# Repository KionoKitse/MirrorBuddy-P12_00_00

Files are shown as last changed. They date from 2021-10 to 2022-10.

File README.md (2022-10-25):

### Description 
A project to automate power mirrors. The system will detect who is driving based on their seat position. From this, the system will automatically adjust the mirror position based on the detected user's known preferences. Additionally the system will be able to learn new settings if a user has decided to manually adjust the mirror position. 

### Hardware in use
* 1X ATmega328 (Arduino Pro Mini)
* 1X YX-X801 (low voltage cutoff)
* 2X ATtiny85 (micro processor)
* 3X L7805CV (voltage regulator)
* 4X OH137 (hall Sensor)
* 3X MAX485 (RS485 communication modules)

### What's next
* Get ATTiny85 to send a number via RS485 and display it on Arduino with OLED
* Get ATTiny85 to send the values in the correct format
* Design circuit boards  
 
### Progress log 
<details>
	<summary>Details of the project history</summary>
	
* 2021-10-05 Started the GitHub repository
* 2021-10-06 OLED test with Pro Mini
* 2021-10-07 Tested transmitting a value from ATtiny85 to ATmega328 over RS485 and displayed with OLED
* 2021-10-13 Building a RS485 HAT to ease testing
* 2021-10-18 Got the plotter working
* 2021-10-18 Monitor hall over serial working fine
* 2022-10-09 Hall sensor reading from spare housing
* 2022-10-10 Working on code to count number of rotations
* 2022-10-10 ATtiny with peakdetection and softserial
* 2022-10-11 Determined that peak detection uses too much memory "Global variables use 489 bytes (95%) of dynamic memory"
* 2022-10-12 Created a simpler peak detection algorithm 
* 2022-10-13 Added a debounce setting to MonitorHall it seems to be sending counts as expected 
* 2022-10-14 Added code to monitor 2 hall sensors 
* 2022-10-16 Built a relay board that can control the motors 
* 2022-10-17 Working on code to control relay board
* 2022-10-24 Soldered the relay board into the wiring harness
* 2022-10-24 There is some issue with the relay board everything shorts to ground when adjusting the switch
* 2022-10-25 Added a KiCad model to the project
</details>

### Notebook
<details>
	<summary>Next steps</summary>
	
* Voltage divider to sense mirror controls
* Test inputs from mirror switch
* Check for noise with 5V regulator on bench
* Check voltage stability in the car with regulator
* Check if we can run without voltage regulators on each mirror
* ProMini turn on motors then turn off after correct number of rotations achieved 
* Test with multiple MAX485 modules on the network
* Build sample module with ATTiny85
</details>

<details>
	<summary>Notes on the project</summary>
	
* Best to have ATTiny85 keep track of count in case ATmega328 misses a count
* Would be nice to see the actual values that got triggered for data monitoring
* RS485 only send a byte so that makes it challenging for sending an int
* Plotting with RS485 seems too slow
* Would be interesting to see if the MAX485 module could do TX/RX might make calibration easier
* Does rail voltage affect the hall sensors? If so then maybe it would be good to only calibrate them after the voltage has stabilized. 
</details>

<details>
	<summary>Overview</summary>
	
- ProMini is the controller
	* It will detect which diver is in the seat
	* It will detect if the driver has adjusted the mirror
	* It will activate the controls to adjust the mirrors to the correct place
	* Data received
		+ The proMini will be receiving a value that is between 0-255 that contains the limit data and count
		+ It will know which ATtiney is sending because it will be controlling the power to the mirrors
		+ It will also know who is sending because it will have a sensor to detect which way the mirror button is pointing if the user is manually adjusting the mirror position
		+ In the case that the magnet stops in front of the hall sensor then the ATtiny will be sending sporadic readings
		+ There will need to be some sort of way to filter out this noise or adjust the mirrors a little bit to avoid this
- ATtiny85 1&2 are the sensors that monitor the position of the mirrors
	* They will send a signal when the limit switches have been activated
	* They will sens a signal when the hall sensors have detected the magnet passing
	* The RS485 sends a byte of data so that 0-255
	* Data sent
		+ 100 is limit switch for sensor 1 is hit
		+ 200 is limit switch for sensor 2 is hit
		+ 150 is 50 rotations on sensor 1 counted
		+ 255 is 55 rotations counted on sensor 2
	* The count on sensors is reset after 2 seconds of not seeing the hall sensor move
	* There should be some way to calibrate the threshold for the hall sensor reading
	* When it gets power (car turned on) the ProMini will move the mirrors to their outer limits
	* While this is happening the ATtiny85 will be recording the values detected
	* The ProMini will stop and wait a few seconds
	* When the ATtiny detects that it hasn't moved in a while it will use a filter on the collected data to determine the cutoff threshold
	* This data will be sent to the ProMini for logging and the threshold will be set
	* After this data has been sent the ProMini will know that it is okay to move the mirrors into possition
</details>

<details>
	<summary>Collision avoidance</summary>
	
- Collisions are avoided because the ProMini will only be controlling one ATtiny85 at a time so only one node will be transmitting at a time
- It would be impossible for both nodes to be transmitting since the user can only move one mirror at a time
</details>

<details>
	<summary>General thoughts</summary>
	
- Having the ProMini being the controller will allow me to make fine adjustments without having to pull the mirrors off
- limit switches
	* It could be problematic to use the limit switches since they could easily get water damaged since they are exposed to the elements quite a lot. It would be beneficial not not have to rely on them.
	* If I was doing this again I would not have added them since I could easily drive the motors out until I'm sure I'm at the outside limit and then work backwards from there.
	* The inside limit puts stress on the plastic nuts but the outside limit does not
	* Perhaps it's better to not use the limits at all
</details>

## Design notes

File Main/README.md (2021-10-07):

### Description 
In this test the ATTiny85 reads the value of the potentiometer and converts it to a value between 1-180. Then it passes this value over the software serial to the MAX485. A MAX485 on the other side gets the number and sends it to at ATmega328p which displays the value on an SPI OLED screen.

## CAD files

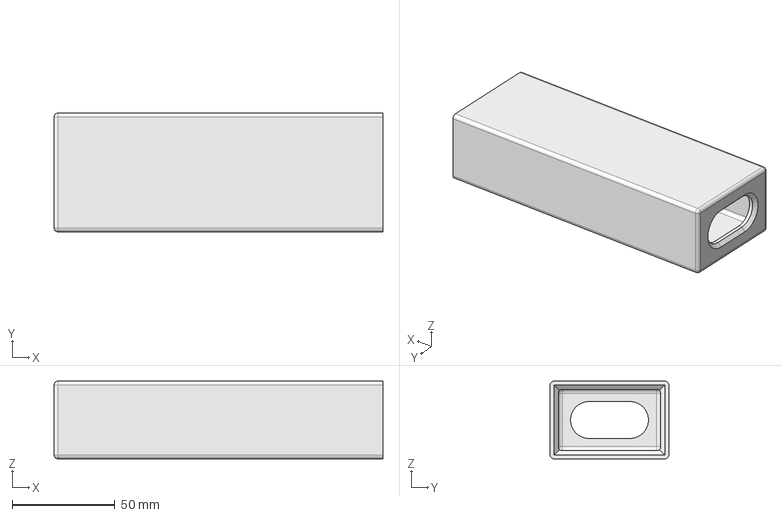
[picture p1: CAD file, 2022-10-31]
Tests/temp/PartB.FCStd
160.5 x 58.0 x 38.0 mm

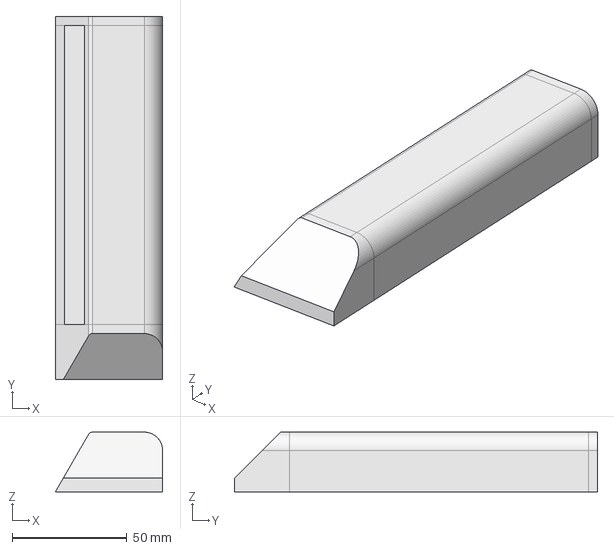
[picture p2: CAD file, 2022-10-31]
Tests/temp/PartA.FCStd
46.7 x 158.0 x 26.0 mm

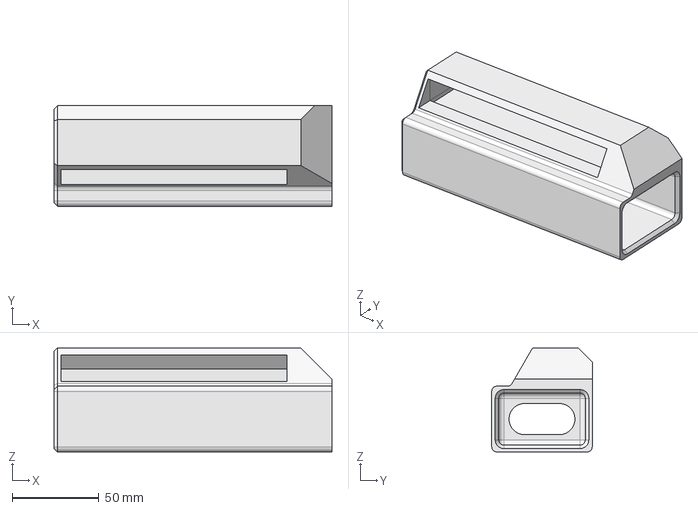
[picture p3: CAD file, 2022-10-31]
Tests/temp/support.FCStd
160.4 x 58.0 x 60.0 mm

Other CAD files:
Tests/temp/PartA.stl
Tests/temp/PartB.stl

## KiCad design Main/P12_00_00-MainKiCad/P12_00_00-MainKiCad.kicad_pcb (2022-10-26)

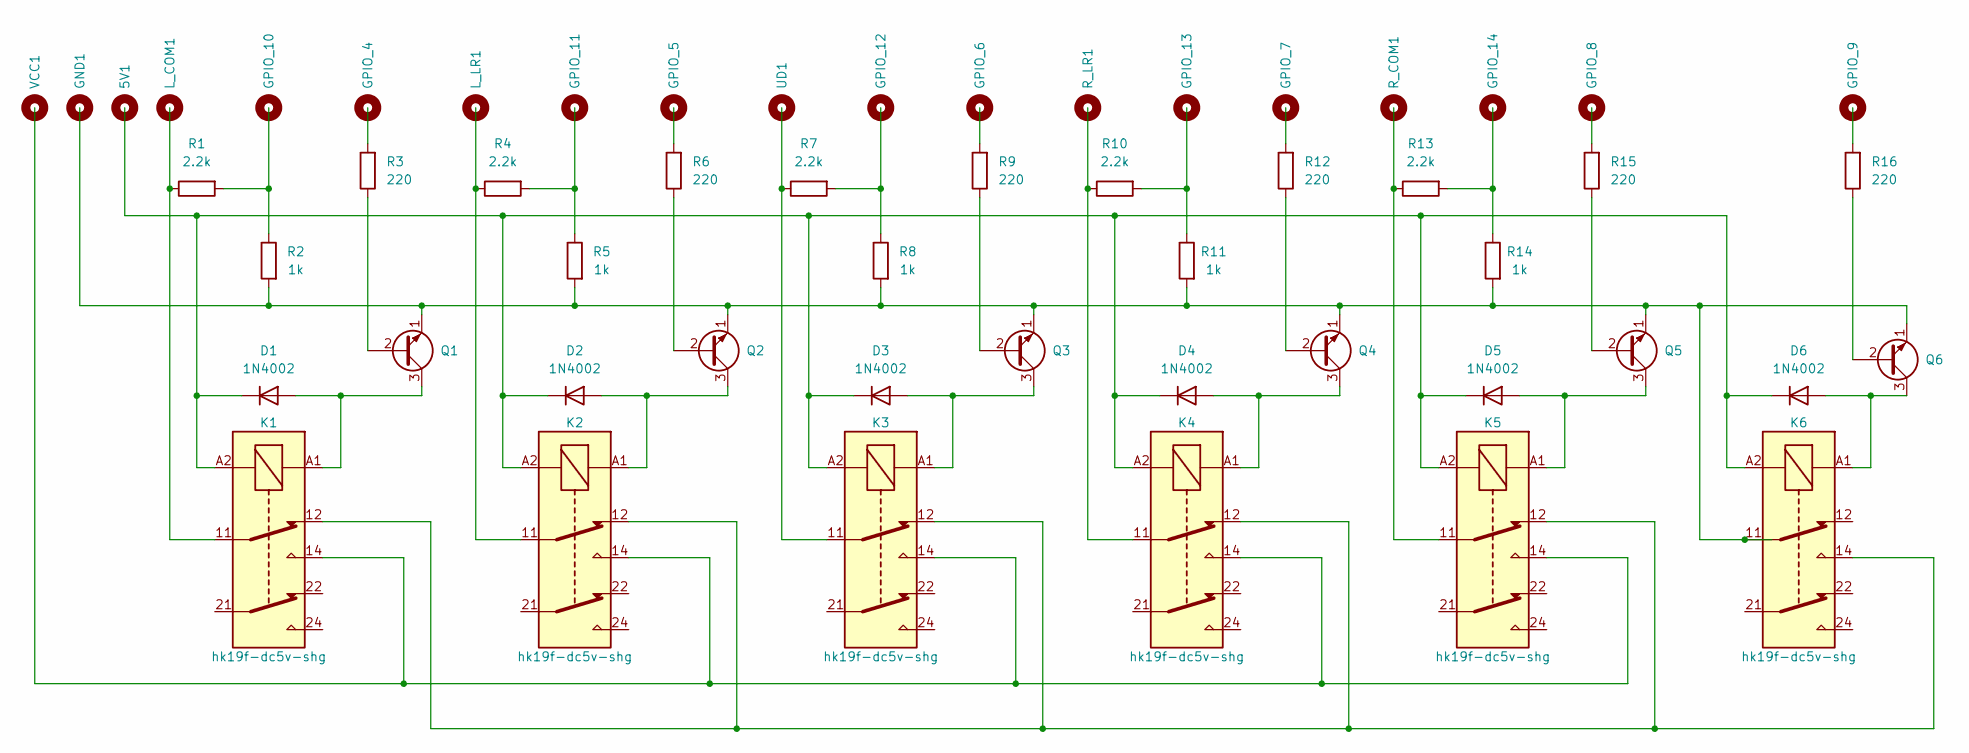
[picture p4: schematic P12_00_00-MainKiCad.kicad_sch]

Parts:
5V1: L_COM; MountingHole_2.1mm
D1, D2, D3, D4, D5, D6: 1N4002; D_DO-34_SOD68_P7.62mm_Horizontal
GND1: L_COM; MountingHole_2.1mm
GPIO_4, GPIO_5, GPIO_6, GPIO_7, GPIO_8, GPIO_9, GPIO_10, GPIO_11, GPIO_12, GPIO_13, GPIO_14: L_COM; MountingHole_2.1mm
K1, K2, K3, K4, K5, K6: hk19f-dc5v-shg; Relay_DPDT_Schrack-RT2-FormC_RM5mm
L_COM1: L_COM; MountingHole_2.1mm
L_LR1: L_COM; MountingHole_2.1mm
Q1, Q2, Q3, Q4, Q5, Q6: 2N3904; TO-92_Inline
R1, R4, R7, R10, R13: 2.2k; R_Axial_DIN0204_L3.6mm_D1.6mm_P5.08mm_Horizontal
R2, R5, R8, R11, R14: 1k; R_Axial_DIN0204_L3.6mm_D1.6mm_P5.08mm_Horizontal
R3, R6, R9, R12, R15, R16: 220; R_Axial_DIN0204_L3.6mm_D1.6mm_P5.08mm_Horizontal
R_COM1: L_COM; MountingHole_2.1mm
R_LR1: L_COM; MountingHole_2.1mm
UD1: L_COM; MountingHole_2.1mm
VCC1: L_COM; MountingHole_2.1mm

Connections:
unnamed: D1.1 (K), D2.1 (K), D3.1 (K), D4.1 (K), D5.1 (K), D6.1 (K), K1.A2, K2.A2, K3.A2, K4.A2, K5.A2, K6.A2
unnamed: D1.2 (A), K1.A1, Q1.3 (C)
unnamed: K1.11, R1.1
unnamed: K1.12, K2.12, K3.12, K4.12, K5.12, K6.14
unnamed: K1.14, K2.14, K3.14, K4.14, K5.14
unnamed: D2.2 (A), K2.A1, Q2.3 (C)
unnamed: D3.2 (A), K3.A1, Q3.3 (C)
unnamed: D4.2 (A), K4.A1, Q4.3 (C)
unnamed: D5.2 (A), K5.A1, Q5.3 (C)
unnamed: D6.2 (A), K6.A1, Q6.3 (C)
unnamed: K6.11, Q1.1 (E), Q2.1 (E), Q3.1 (E), Q4.1 (E), Q5.1 (E), Q6.1 (E), R2.2, R5.2, R8.2, R11.2, R14.2
unnamed: Q1.2 (B), R3.1
unnamed: Q6.2 (B), R16.1
unnamed: R1.2, R2.1
unnamed: K2.11, R4.1
unnamed: R4.2, R5.1
unnamed: Q2.2 (B), R6.1
unnamed: K3.11, R7.1
unnamed: R7.2, R8.1
unnamed: Q3.2 (B), R9.1
unnamed: K4.11, R10.1
unnamed: R10.2, R11.1
unnamed: Q4.2 (B), R12.1
unnamed: K5.11, R13.1
unnamed: R13.2, R14.1
unnamed: Q5.2 (B), R15.1

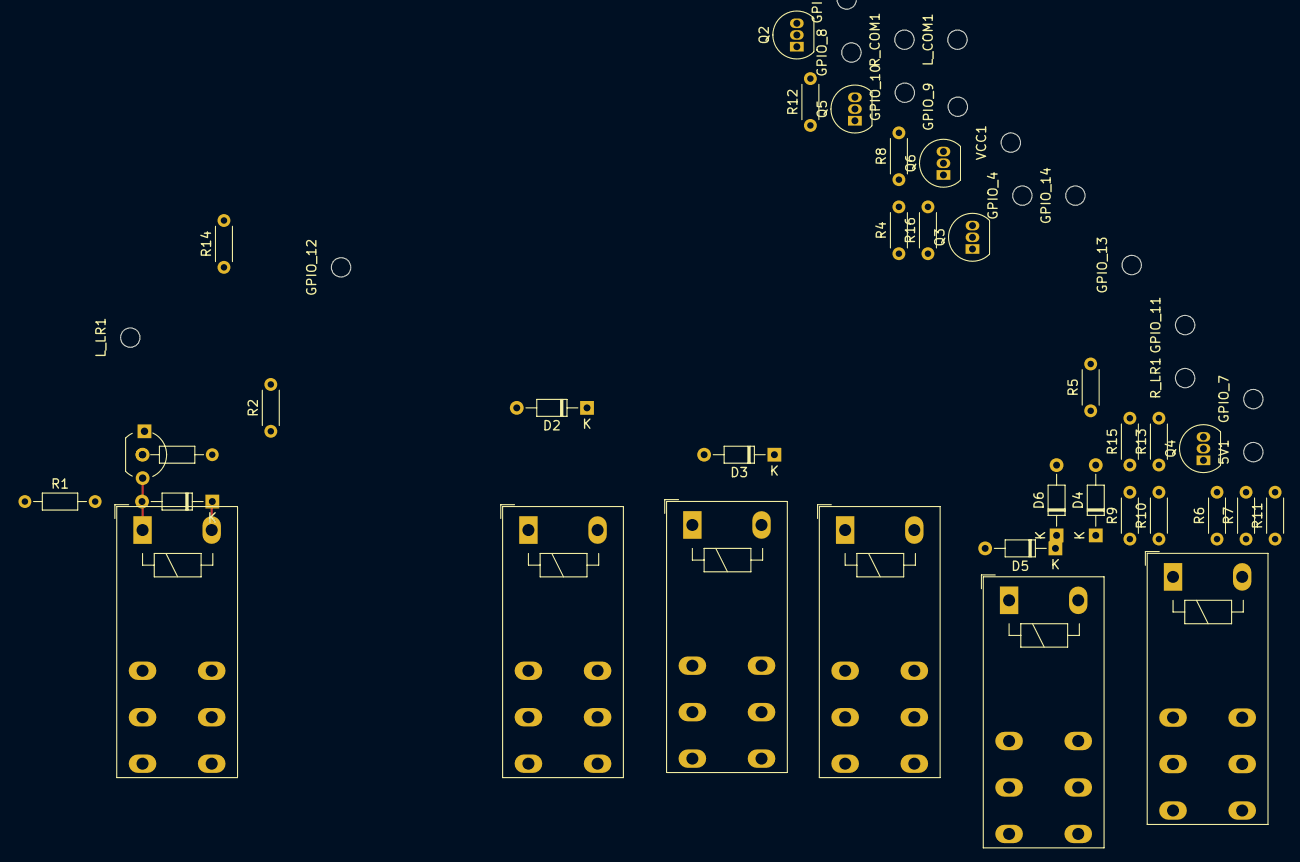
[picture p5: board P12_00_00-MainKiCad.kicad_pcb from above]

Board: 2 copper layers, 53 parts (0 on the bottom side), 26 nets.

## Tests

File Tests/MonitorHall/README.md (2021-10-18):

### Description 
In this test the ATTiny85 reads the value of the potentiometer and converts it to a value between 0-255. Then it passes this value over the software serial to the MAX485. A MAX485 on the other side gets the number and converts it back into the 0-1024 range and prints the value to the Serial Monitor.

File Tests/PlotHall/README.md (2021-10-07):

### Description 
In this test the ATtiny85 is connected to a hall sensor as well as an RS485 module. The sensor will read the hall sensor and stream the values to an ATmega328 with a RS485 module and a OLED screen. The ATmega328 will plot the values on the display. Ideally this can be used to visualize the hall sensor data and set appropriate limits.

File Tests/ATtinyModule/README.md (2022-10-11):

### Description 
This program is the testing place for the Main program as it relates to the ATtiny85 

### Test modes
1. Estimate cutoff threshold
	* Record values in array
	* If no values for more than 2 seconds
		* 2 STD is the threshold
		* Send array and threshold
2. Count rotations
3. Send counts

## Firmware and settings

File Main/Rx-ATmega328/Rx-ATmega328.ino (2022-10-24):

/*
   P12_00_00-Main
   Project: P12_00_00 MirrorBuddy
   
   Notes:
   * This is the code that is running on Pro Mini
   * It is intended to control the motors and monitor the sensors in the mirrors
   * Circuit Js: https://tinyurl.com/2ms5rb3e

   Connections
   PIN   - FUNC - CONNECTION
   Pin 01 - Tx0 - N/C
   Pin 02 - Rx1 - N/C
   Pin 03 - RST - N/C
   Pin 04 - GND - GND
   Pin 05 - D2  - N/C
   Pin 06 - D3  - N/C
   Pin 07 - D4  - RelayA
   Pin 08 - D5  - RelayB
   Pin 09 - D6  - RelayC
   Pin 10 - D7  - RelayD
   Pin 11 - D8  - RelayE
   Pin 12 - D9  - RelayF
   Pin 13 - GND - N/C
   Pin 14 - A6  - N/C
   Pin 15 - A7  - N/C
   Pin 16 - D10 - L_COM
   Pin 17 - D11 - L_LR
   Pin 18 - D12 - UD
   Pin 19 - D13 - R_LR
   Pin 20 - A0  - R_COM
   Pin 21 - A1  - N/C
   Pin 22 - A2  - N/C
   Pin 23 - A3  - N/C
   Pin 24 - A4  - N/C
   Pin 25 - A5  - N/C
   Pin 13 - VCC - 5V Out
   Pin 13 - RST - N/C
   Pin 13 - GND - N/C
   Pin 13 - RAW - 5V RAW

   Hardware
   * 1X ATmega328
   * 1X MAX485 TTL to RS-485
   * 6X Relay
   * 6X Transistor
   * 6x Resistor
   * 12X 1k Resistor

   Credits
   * https://forum.arduino.cc/t/rs485-simple-integer-transfer/619544/13
*/

//MAX485
#include <SoftwareSerial.h>
SoftwareSerial mySerial(0,4);  //rx, tx TBD
byte byteData;
byte extractedData;

//Settings
int limitDelay = 2000;  //The amount of time to move a mirror into it's outer most limmit. This is also the time where the sensors are calibrated.
int configTime = 6000;  //Time to aquire max, min values from hall sensors
int resetTime = 4000;   //If no peaks are detected after this time, the count gets reset
int debounceTime = 200; //Time to ignore input for debounce
int syncOffset = 500;   //Slight time offset so both mirrors don't transmit at the same time
byte debug = true;      //Enable debug output


//Global variables (Relay Patterns)
bool L_UP[]   = {0,0,1,1,1,1};
bool L_DOWN[] = {1,1,0,0,0,1};
bool L_LEFT[] = {1,0,1,1,1,1};
bool L_RIGHT[]= {0,1,0,0,0,1};
bool R_UP[]   = {1,1,1,0,0,1};
bool R_DOWN[] = {0,0,0,1,1,1};
bool R_LEFT[] = {1,1,1,0,1,1};
bool R_RIGHT[]= {0,0,0,1,0,1};
bool LR_UP[]  = {0,0,1,0,0,1};

//Global variables (Counting Roations)
char user, lastUser;                                              //Variables to hold which user is present
byte mirrorLDirL, mirrorLDirD, mirrorRDirR, mirrorRDirD;          //Variable to hold the requested number of counts
byte ctMirrorLDirL, ctMirrorLDirD, ctMirrorRDirR, ctMirrorRDirD;  //Variable to hold the current number of counts



void setup()
{
  //Serial
  if(debug)Serial.begin(9600);
  mySerial.begin(9600);

  //Set relay pins as output
  for(byte i=4; i<10; i++){
    pinMode(i,OUTPUT);
    digitalWrite(i,0);
  }

  //Set motor sensor pins as input
  for(byte i=10; i<15; i++){
    pinMode(i,INPUT);
  }

  //Move left mirror to right limit
  if(debug)Serial.println("L_RIGHT");
  SetRelays(L_RIGHT);
  delay(limitDelay);
  ClearRelays();   

  //Move right mirror to left limit
  if(debug)Serial.println("R_LEFT");
  SetRelays(R_LEFT);
  delay(limitDelay);
  ClearRelays(); 

  //Move both mirrors up
  if(debug)Serial.println("LR_UP");
  SetRelays(LR_UP);
  delay(limitDelay);
  ClearRelays(); 

  //Check user and get settings
  if(debug)Serial.println("UserA");
  user = 'A';
  if(user == 'A'){
    mirrorLDirL = 20;
    mirrorLDirD = 30;
    mirrorRDirR = 40;
    mirrorRDirD = 20;
  }
  ctMirrorLDirL = 0;
  ctMirrorLDirD = 0;
  ctMirrorRDirR = 0;
  ctMirrorRDirD = 0;

  //Set left mirror
  if(debug)Serial.println("Set left mirror down");
  SetRelays(L_DOWN);
  while(ctMirrorLDirD <= mirrorLDirD){
    if(mySerial.available()){
      byteData = mySerial.read();
      if(byteData < 127){
        extractedData = byteData; //For the up/down direction the value can only be between (0 <= countA < 127) 
        ctMirrorLDirD = extractedData;
        if(debug){
          Serial.print(byteData);
          Serial.print(",");
          Serial.println(extractedData);
        }
      }
    }
  }
  ClearRelays(); 
  if(debug)Serial.println("Set left mirror left");
  SetRelays(L_LEFT);
  while(ctMirrorLDirL <= mirrorLDirL){
    if(mySerial.available()){
      byteData = mySerial.read();
      if(byteData >= 127){
        extractedData = byteData-127; //For the left/right direction the value can only be between (127 <= countB < 255) 
        ctMirrorLDirD = extractedData;
        if(debug){
          Serial.print(byteData);
          Serial.print(",");
          Serial.println(extractedData);
        }
      }
    }
  }
  ClearRelays(); 

  if(debug)Serial.println("Set right mirror down");
  SetRelays(R_DOWN);
  while(ctMirrorRDirD <= mirrorRDirD){
    if(mySerial.available()){
      byteData = mySerial.read();
      if(byteData < 127){
        extractedData = byteData; //For the up/down direction the value can only be between (0 <= countA < 127) 
        ctMirrorLDirD = extractedData;
        if(debug){
          Serial.print(byteData);
          Serial.print(",");
          Serial.println(extractedData);
        }
      }
    }
  }
  ClearRelays(); 
  if(debug)Serial.println("Set right mirror right");
  SetRelays(R_RIGHT);
  while(ctMirrorRDirR <= mirrorRDirR){
    if(mySerial.available()){
      byteData = mySerial.read();
      if(byteData >= 127){
        extractedData = byteData-127; //For the left/right direction the value can only be between (127 <= countB < 255) 
        ctMirrorLDirD = extractedData;
        if(debug){
          Serial.print(byteData);
          Serial.print(",");
          Serial.println(extractedData);
        }
      }
    }
  }
  ClearRelays(); 

  if(debug)Serial.println("Mirrors Set");

  
  
  
}

void loop()
{


}

void SetRelays(bool arraySet[6]){
  for(byte i=0; i<6; i++){
    digitalWrite(i+4,arraySet[i]);
    Serial.print(arraySet[i]);
    Serial.print(",");
  }
  Serial.println();
}
void ReadSensors(){
  for (byte i=10; i<15;i++){
    Serial.print(digitalRead(i));
    Serial.print(",");
  }
  Serial.println("");
  Serial.println("");
}
void ClearRelays(){
  for(byte i=4; i<10; i++){
    digitalWrite(i,0);
  }
}

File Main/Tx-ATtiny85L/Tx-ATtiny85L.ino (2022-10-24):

/*
   P12_00_00-Main
   Project: P12_00_00 MirrorBuddy
   
   Notes:
   * This is the code that is running on the ATtiny85 in the left mirror housing
   * The code is slightly different for the other mirror to prevent collisions on RS485

   Connections
   PIN   - FUNC  - CONNECTION
   Pin 1 - Reset - N/C
   Pin 2 - A3/D3 - OH137 A Up
   Pin 3 - A2/D4 - MAX485(DI)
   Pin 4 - GND   - GND
   Pin 5 - D0    - N/C
   Pin 6 - D1    - N/C
   Pin 7 - A1/D2 - OH137 B Right
   Pin 8 - VCC   - VCC

   Hardware
   * 2X OH137
   * 1X MAX485 TTL to RS-485
   * 1X ATtiny85

   Credits
   * https://forum.arduino.cc/t/rs485-simple-integer-transfer/619544/13
*/

//MAX485
#include <SoftwareSerial.h>
SoftwareSerial mySerial(0,4);  //rx, tx

//Settings
int configTime = 6000;  //Time to aquire max, min values from hall sensors
int resetTime = 4000;   //If no peaks are detected after this time, the count gets reset
int debounceTime = 200; //Time to ignore input for debounce
int syncOffset = 500;   //Slight time offset so both mirrors don't transmit at the same time

//Define pins
#define hallA         A3  //Data pin of the hall sensor monitoring the up/down direction motor
#define hallB         A1  //Data pin of the hall sensor monitoring the right/left direction motor

//Global variables (Peak Detection)
long refTime;
int maxValA, minValA, thresholdA, sensorValA;
int maxValB, minValB, thresholdB, sensorValB;
bool peakA, lastPeakA;
bool peakB, lastPeakB;

//Global variables (Rotation Counting)
byte countA, countB;
long lastCountA, lastCountB;

void setup() 
{ 
  //Serial
  mySerial.begin(9600);

  //General pin setup
  pinMode(hallA, INPUT);
  pinMode(hallB, INPUT);

  //Variable setup
  lastPeakA = 0;
  lastPeakB = 0;
  countA = 0;
  countB = 0;
  lastCountA = millis();
  lastCountB = millis();

  //Calculate threshold values
  maxValA = 0;
  maxValB = 0;
  minValA = 1023;
  minValB = 1023;
  refTime = millis();
  while((millis()-refTime) < configTime){
    sensorValA = analogRead(hallA);
    sensorValB = analogRead(hallB);
    if(sensorValA > maxValA) maxValA = sensorValA;
    if(sensorValA < minValA) minValA = sensorValA;
    if(sensorValB > maxValB) maxValB = sensorValB;
    if(sensorValB < minValB) minValB = sensorValB;
  }
  thresholdA = ((maxValA-minValA)/2)+minValA; 
  thresholdB = ((maxValB-minValB)/2)+minValB; 
  
  //Set counts (note: (0 <= countA < 127) & (127 <= countB < 255))
  countA = 0; 
  countB = 127; 

  //Send ready command
  delay(syncOffset);
  mySerial.write(countA); 
  mySerial.write(countB); 
} 
 
void loop() 
{ 
  //Only read from sensor after the debounce time
  if((millis()-lastCountA) > debounceTime){
    //Read from sensor
    sensorValA = analogRead(hallA);
    
    //Peak detection
    peakA = ( sensorValA > thresholdA ) ? 1 : 0;

    //Counting
    if ((peakA > 0) && (lastPeakA != 1)){
      countA++;
      lastCountA=millis();
      
      //Send count 
      mySerial.write(countA); 
    }
    lastPeakA = peakA;

    //Timeout reset count
    if((millis()- lastCountA) > resetTime) countA = 0; 
  
    //Rollover reset count
    if(countA > 125) countA = 0;
  } 

  
  //Only read from sensor after the debounce time
  if((millis()-lastCountB) > debounceTime){
    //Read from sensor
    sensorValB = analogRead(hallB);
    
    //Peak detection
    peakB = ( sensorValB > thresholdB ) ? 1 : 0;

    //Counting
    if ((peakB > 0) && (lastPeakB != 1)){
      countB++;
      lastCountB=millis();
      
      //Send count 
      mySerial.write(countB); 
    }
    lastPeakB = peakB;

    //Timeout reset count
    if((millis()- lastCountB) > resetTime) countB = 127;
  
    //Rollover reset count
    if(countB > 254) countB = 127;
  }  
}

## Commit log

2021-10-07 OLED test
    [OLED-HelloWorld.fzz]
2021-10-07 Save point PlotHall
    [PlotHall.fzz]
2021-10-13 Working to send int over RS485
    [RS485-SendInt.fzz]
2021-10-13 Working on main circuit
    [Main.fzz]
2021-10-18 Main circuit
    [Main.fzz]
2021-10-18 Monitor Hall Sketch
    [MonitorHall.fzz]
2022-09-26 Test program for ATtiny85 module
    [ATtinyModule.fzz]
2022-10-11 Working on peak detection with ATtiny85 and MAX485
    Peak detection and max485 aren't working together I suspect that I'm running out of memory so I might need a different peak detection or soft serial
    [MonitorHall.fzz]
2022-10-14 Added code to monitor 2 hall sensors
2022-10-17 Working on motor controller
    [MotorTest.fzz]
2022-10-17 Code to support the relay board
2022-10-25 Added a KiCad model to the project
    [P12_00_00-MainKiCad.kicad_pcb, P12_00_00-MainKiCad.kicad_sch]
2022-10-26 KiCAD modifications
    [P12_00_00-MainKiCad.kicad_pcb, P12_00_00-MainKiCad.kicad_sch]
2022-10-31 Working with the schematic
    [MotorTest.fzz, P12_00_00-MainKiCad.kicad_sch, PartA.FCStd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]
